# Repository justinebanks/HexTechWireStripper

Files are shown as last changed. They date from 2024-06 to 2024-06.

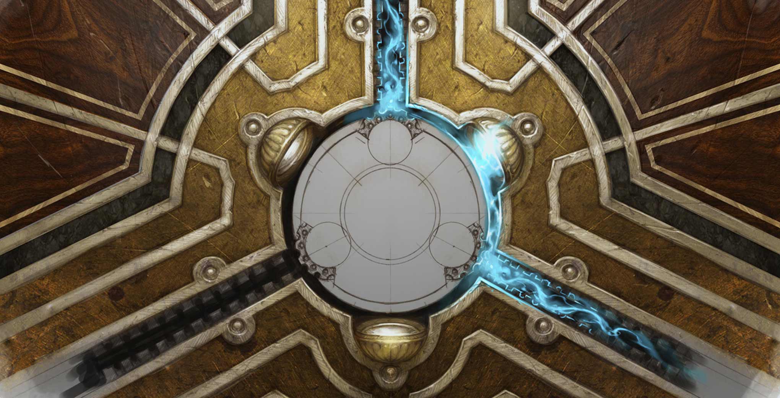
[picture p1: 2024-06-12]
src/web/HexTech_LoL.jpg

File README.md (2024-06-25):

# HexTechAutoWireStripper
---

### Explanation
This project is a machine built to automatically cut and strip wires. This project was inspired by Programming with Red's version of it, but has been changed to work with the HexTech circuit board.

### MQTT Server
The HexTech circuit board is subscribed to an [MQTT server](https://mqtt.org/) in the cloud. The software can send publish messages to the server and the HexTech board's ESP32 microcontroller will recieve it and run the command specified. In Javascript, I used the MQTT.js CDN to very easily connect to the server.

The problem, though, was that the HexTech board wouldn't recieve a command if the command string contained too many commands. To bypass this, I had to send bits of the commands separated by 2 second delays. To do this, I translated my code to Java and used Java Swing instead of HTML, CSS, & Javascript. Because of this the full finished project is within the src/java directory

### Project Organization
The src directory contains to main parts: web and java. The user interface for this project was meant to be in the form of a website, but a problem with the MQTT Server led me to switch to Java.

The src/java direcory is a Maven project that can be downloaded and built with the VSCode "Extension Pack for Java" plugin. Any YouTube tutorial on Maven in VSCode will help get you started.

The src/web directory contains the old relic that is the Javascript project. If you open it in the browser, though, you can accessGoogle Chrome's DevTools Console by pressing Ctrl+Shift+I and navigating to the console window. This gives you access to 2 important functions for debugging: ```moveTopBlade(int)``` and ```moveWire(int)```. If the 2 linear motion motors become unbalanced, it can be fixed by running ```runSerialCommand("stepper.00_move_400")``` to move the left side down to use the other 2 functions, you need to pass their output to the ```runSerialCommand(String)``` function

### Testing and Debugging
In addition to using the DevTools Console to debug, the Java Project has an MqttTester class, which is instatiating in the MqttConnector file. By running MqttConnector.java, it will open a simple GUI application where you can manually send commands to the HexTech board through the MQTT server.

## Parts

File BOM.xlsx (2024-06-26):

Name | Quantity | Price | Notes
HexTech Board | 1 | N/A | The circuit board that makes the machine compatible with the application
Small Stepper Motor | 3 | ~$15
Wooden Board | 1 | N/A | Optional. Any Board that the components can be screwed onto works
Power Source | 1 | N/A | Preferably the HexTech-designated power source, but can be anything
WORKPRO Utility Knife Blades | 1 pack | $10 (https://www.amazon.com/WORKPRO-Utility-Blades-Dispenser-100-pack/dp/B015W3AKDQ?hvadid=693128203622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) | This is the specific blade that fits into the housing
Extruder | 1 | N/A | Can be taken from a 3D printer. These can still be bought, though
Lead screw w/ Copper Nut | 2 | $33 (https://www.amazon.co.uk/dp/B07QWKG317?ref_=cm_sw_r_cp_ud_dp_JMAC4EKE28W5Z3GSZSN8) | Can be attached to the motors with shaft couplers, but are unnecessary if the motors come with one already attached
Shaft Coupler | 2 | ~$20 | Optional. Only needed if the motors don't come with pre-attached lead screws
3D Parts | 7 | N/A | Can be downloaded from the /3d_models folder

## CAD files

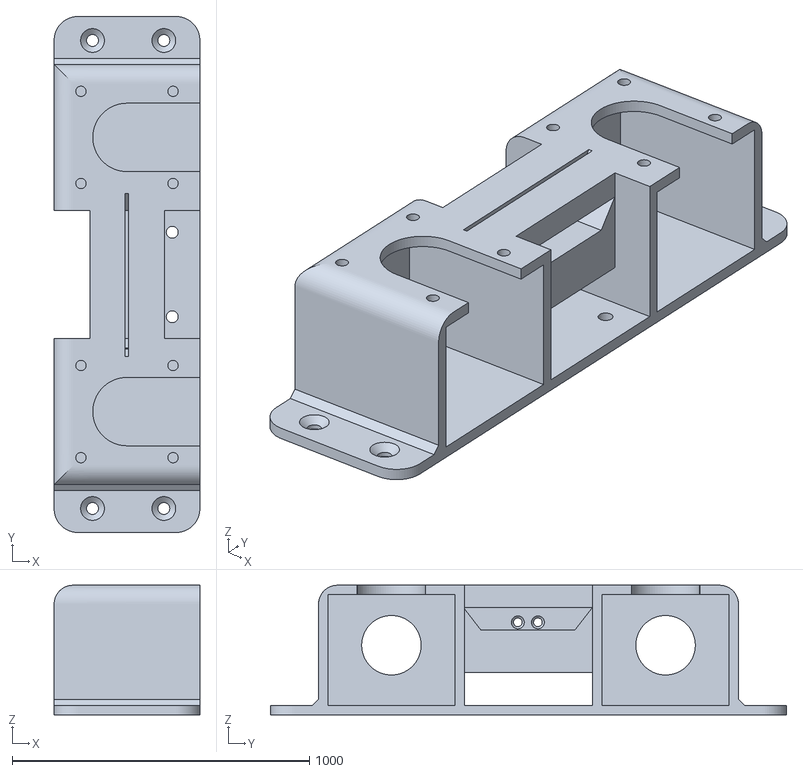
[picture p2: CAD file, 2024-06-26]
3d_models/BottomBladeHousing.stl
490.5 x 1736.0 x 436.0

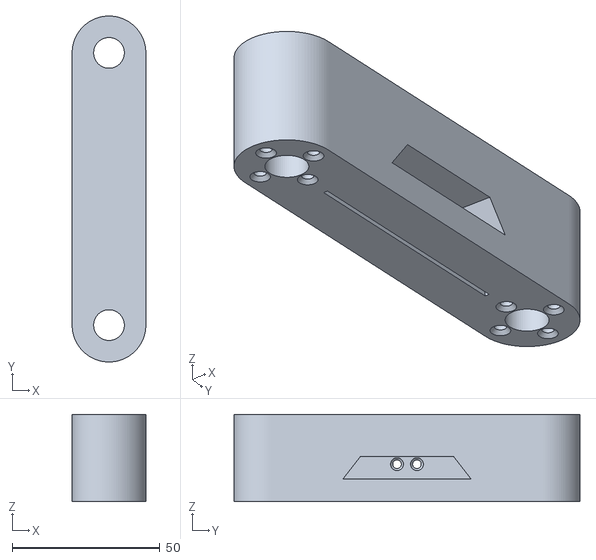
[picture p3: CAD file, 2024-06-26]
3d_models/LinearMotion_Attachment_Justin.stl
25.0 x 117.2 x 29.6

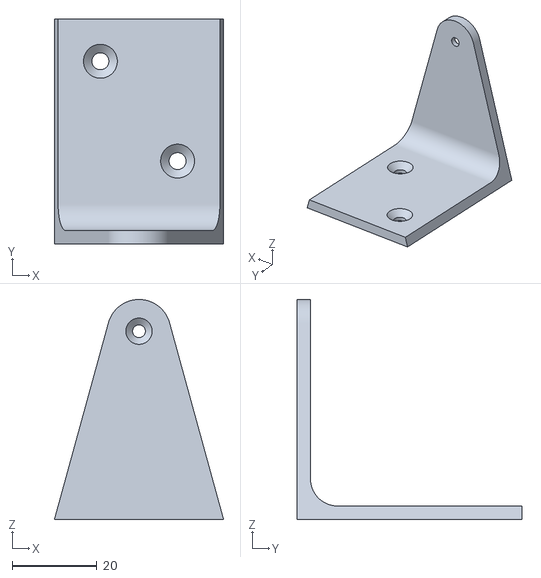
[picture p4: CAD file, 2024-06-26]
3d_models/spoolHolder_base.stl
40.0 x 53.2 x 52.0

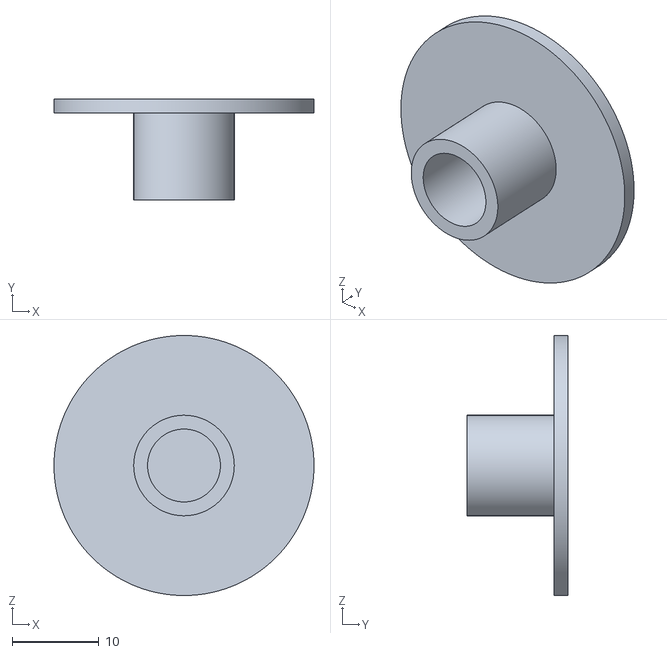
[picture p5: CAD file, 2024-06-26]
3d_models/spoolHolder_cylinder_cap.stl
30.0 x 11.6 x 30.0

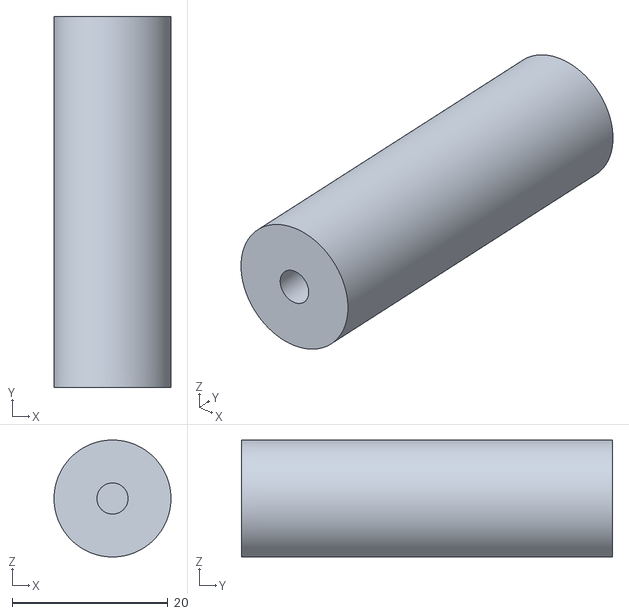
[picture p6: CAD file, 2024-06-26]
3d_models/spoolHolder_cylinder.stl
15.0 x 47.6 x 15.0

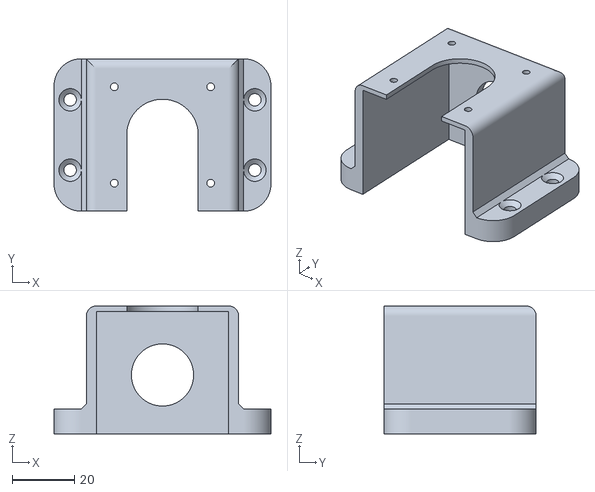
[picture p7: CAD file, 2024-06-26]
3d_models/extruderStepper_housing.stl
69.9 x 49.1 x 41.2

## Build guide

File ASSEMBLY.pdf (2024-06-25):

## Automatic Wire Cutter – Assembly Information

### Stepper Motors

This machine was built using stepper motors. Two of the stepper motors are responsible for the linear motion of the blade and the last motor powers the extruder that moves the wire forward and backward.

### 3D Printing

Most of the 3D printed parts are responsible for housing, but there are 3 spool-holding parts that are responsible for holding the spool of the wire in place. Additionally, there is a pipe glued to the back end of the extruder to keep the wire from bending away from the blade.

### HexTech Circuit Board

Each motor is connected to the HexTech circuit board on the back side of the wooden board. The program that runs the machine is set up to function correctly only if the extruder stepper is plugged into the “stepper 2” output and the stepper motors are connected (from left to right) to the “stepper 0” and “stepper 1” outputs respectively.

### Pictures

Front | Side | _

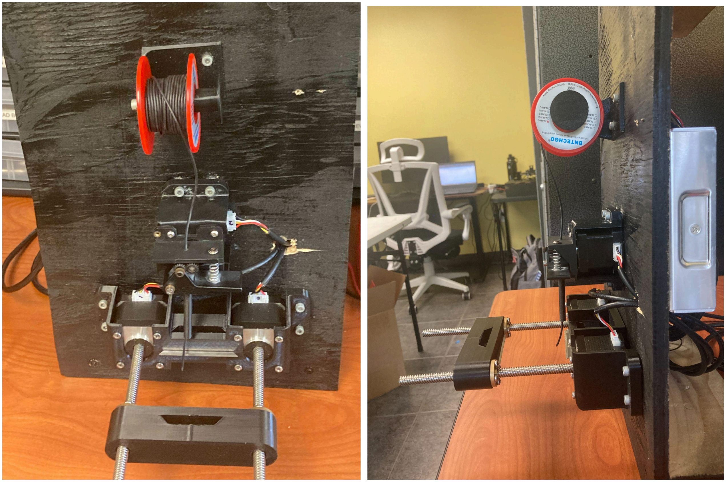
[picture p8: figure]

Back | Diagonal | _

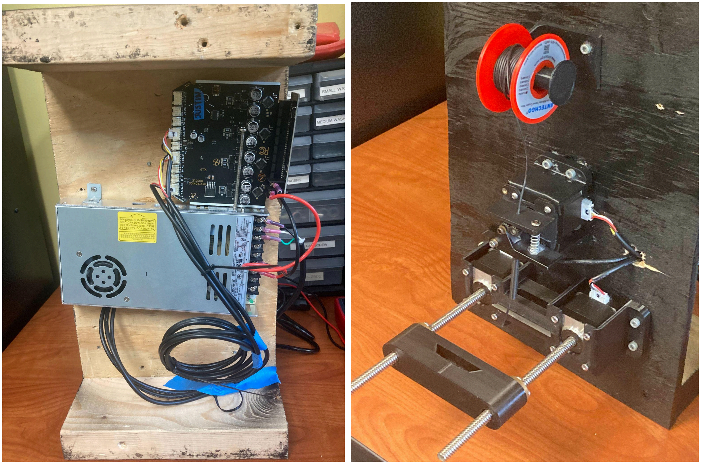
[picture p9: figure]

Wide | _

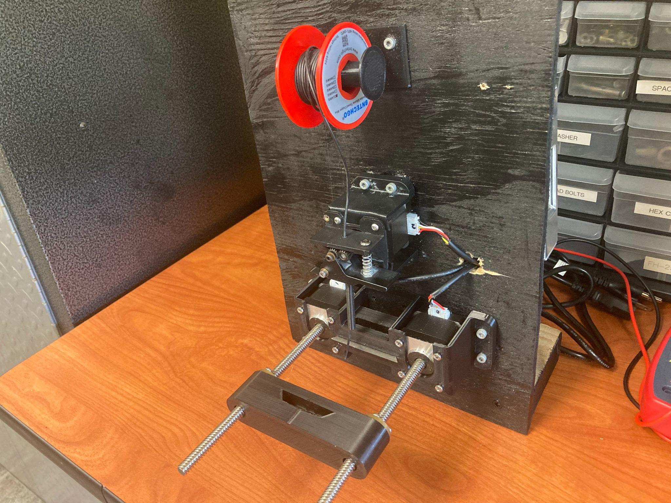
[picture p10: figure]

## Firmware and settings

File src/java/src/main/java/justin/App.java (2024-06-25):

package justin;

import javax.swing.JFrame;
import javax.swing.JTextField;
import javax.swing.SpringLayout;
import javax.swing.JButton;
import javax.swing.JLabel;

import java.awt.Dimension;
import java.awt.event.ActionEvent;
import java.awt.event.ActionListener;

import java.util.ArrayList;
import java.util.concurrent.TimeUnit;


public class App extends JFrame implements ActionListener {

    final String LIN_MOT_ONE = "stepper.00"; // rywb4-rwyb6
    final String LIN_MOT_TWO = "stepper.01"; // bwyr4-rwyb6
    final String EXTRUDER_STEPPER = "stepper.02"; // rywb4-rywb6

    final int LIN_MOT_STEP_DIST = 1;
    final int EXTRUDER_STEP_DIST = 1;
    final int BOTTOM_BLADE_POSITION = -7000;

    ArrayList<String> commandArray = new ArrayList<String>();
    ArrayList<Integer> bladeHistory = new ArrayList<Integer>();

    // MQTT Information
    MqttConnector mqtt = new MqttConnector("ws://mqtt.hextronics.cloud:8083/mqtt", "hextech-justin", "justin");
    String mqttTopic = "hextech/hextech-justin/commands";

    // Global Spring Components
    SpringLayout layout = new SpringLayout();
    JButton submitButton = new JButton("Submit");

    JTextField inputBox = new JTextField();
    JTextField leftStripLength = new JTextField("1000");
    JTextField wireLength = new JTextField("2000");
    JTextField rightStripLength = new JTextField("1000");
    JTextField stripDepth = new JTextField("150");
    JTextField wireQuantity = new JTextField("1");

    JLabel lslLabel = new JLabel("Left Strip Length:");
    JLabel wlLabel = new JLabel("Wire Length:");
    JLabel rslLabel = new JLabel("Right Strip Length:");
    JLabel sdLabel = new JLabel("Strip Depth:");
    JLabel wqLabel = new JLabel("Wire Quantity:");

    public static void main(String[] args) {
        App app = new App();
        String message = "bldc.00_move_5000";

        app.initializeCurrent();
        app.mqtt.publishMessage(app.mqttTopic, message);
        //app.runProgram();
    }


    public App() {
        this.setPreferredSize(new Dimension(540, 360));
        this.setLayout(layout);
        this.setLocationRelativeTo(null);

        Dimension preferredSize = new Dimension(200, 20);
        leftStripLength.setPreferredSize(preferredSize);
        wireLength.setPreferredSize(preferredSize);
        rightStripLength.setPreferredSize(preferredSize);
        stripDepth.setPreferredSize(preferredSize);
        wireQuantity.setPreferredSize(preferredSize);

        submitButton.addActionListener(this);

        addComponents();
        manageLayout();

        this.pack();
        this.setVisible(true);
    }


    private void manageLayout() {
        layout.putConstraint(SpringLayout.NORTH, lslLabel, 40, SpringLayout.NORTH, this);
        layout.putConstraint(SpringLayout.WEST, lslLabel, 80, SpringLayout.WEST, this);
        layout.putConstraint(SpringLayout.NORTH, leftStripLength, 0, SpringLayout.NORTH, lslLabel);
        layout.putConstraint(SpringLayout.WEST, leftStripLength, 50, SpringLayout.EAST, lslLabel);

        layout.putConstraint(SpringLayout.NORTH, wlLabel, 40, SpringLayout.NORTH, lslLabel);
        layout.putConstraint(SpringLayout.WEST, wlLabel, 0, SpringLayout.WEST, lslLabel);
        layout.putConstraint(SpringLayout.NORTH, wireLength, 0, SpringLayout.NORTH, wlLabel);
        layout.putConstraint(SpringLayout.WEST, wireLength, 0, SpringLayout.WEST, leftStripLength);

        layout.putConstraint(SpringLayout.NORTH, rslLabel, 40, SpringLayout.NORTH, wlLabel);
        layout.putConstraint(SpringLayout.WEST, rslLabel, 0, SpringLayout.WEST, lslLabel);
        layout.putConstraint(SpringLayout.NORTH, rightStripLength, 0, SpringLayout.NORTH, rslLabel);
        layout.putConstraint(SpringLayout.WEST, rightStripLength, 0, SpringLayout.WEST, leftStripLength);

        layout.putConstraint(SpringLayout.NORTH, sdLabel, 40, SpringLayout.NORTH, rslLabel);
        layout.putConstraint(SpringLayout.WEST, sdLabel, 0, SpringLayout.WEST, lslLabel);
        layout.putConstraint(SpringLayout.NORTH, stripDepth, 0, SpringLayout.NORTH, sdLabel);
        layout.putConstraint(SpringLayout.WEST, stripDepth, 0, SpringLayout.WEST, leftStripLength);

        layout.putConstraint(SpringLayout.NORTH, wqLabel, 40, SpringLayout.NORTH, sdLabel);
        layout.putConstraint(SpringLayout.WEST, wqLabel, 0, SpringLayout.WEST, lslLabel);
        layout.putConstraint(SpringLayout.NORTH, wireQuantity, 0, SpringLayout.NORTH, wqLabel);
        layout.putConstraint(SpringLayout.WEST, wireQuantity, 0, SpringLayout.WEST, leftStripLength);

        layout.putConstraint(SpringLayout.NORTH, submitButton, 50, SpringLayout.NORTH, wqLabel);
        layout.putConstraint(SpringLayout.WEST, submitButton, 0, SpringLayout.WEST, lslLabel);
    }


    private void addComponents() {
        this.add(lslLabel);
        this.add(wlLabel);
        this.add(rslLabel);
        this.add(sdLabel);
        this.add(wqLabel);

        this.add(leftStripLength);
        this.add(wireLength);
        this.add(rightStripLength);
        this.add(stripDepth);
        this.add(wireQuantity);

        this.add(submitButton);
    }


    @Override
    public void actionPerformed(ActionEvent e) {
        runProgram();
    }


    public void initializeCurrent() {
        mqtt.publishMessage(mqttTopic, "stepper.00_rms_600;stepper.01_rms_600;stepper.02_rms_200");
    }


    public void emergencyStop() {
        mqtt.publishMessage(mqttTopic, "P_stepper.00_stop;P_stepper.01_stop;P_stepper.02_stop");
    }


    public int getBladeRelativePosition() {
        int distFromHome = 0;
    
        for (int i = 0; i < bladeHistory.size(); i++) {
            distFromHome += bladeHistory.get(i);
        }
    
        return distFromHome;
    }


    public void goHome() {
        mqtt.publishMessage(mqttTopic, moveTopBlade(-getBladeRelativePosition()));
        bladeHistory.clear();
    }


    public String commandArrayToString() {
        String returnString = "";
    
        for (int i = 0; i < commandArray.size(); i++) {
            returnString = returnString + "|" + commandArray.get(i);
        }
    
        return returnString;
    }


    public String moveTopBlade(int distance) { // Positive for Up, Negative for Down
        int dist = LIN_MOT_STEP_DIST * distance;
        String command = String.format("%1$s_move_%2$d;%3$s_move_%4$d", LIN_MOT_ONE, dist*-1, LIN_MOT_TWO, dist);
    
        commandArray.add(command);
        bladeHistory.add(distance);
    
        return command;
    }


    public String moveWire(int distance) { // Positive for Forward, Negative for Backward
        int dist = EXTRUDER_STEP_DIST * distance;
        String command = String.format("%1$s_move_%2$d", EXTRUDER_STEPPER, dist);
        commandArray.add(command);
    
        return command;
    }


    public String cutWire() {
        return moveTopBlade(BOTTOM_BLADE_POSITION - getBladeRelativePosition());
    }
    
    
    public String stripWire() {
        return moveTopBlade(BOTTOM_BLADE_POSITION - getBladeRelativePosition() + Integer.parseInt(stripDepth.getText()));
    }
    
    
    public void testSequence() {
        commandArray.clear();
        moveWire(2000);
        moveTopBlade(-5000);
        moveWire(-1500);
        moveTopBlade(5000);

        mqtt.publishMessage(mqttTopic, commandArrayToString());
    }


    // Segments the full command into 3 parts and runs them separately with a 
    public void runProgram() {
        commandArray.clear();
        moveWire(Integer.parseInt(leftStripLength.getText()));
        stripWire();
        moveTopBlade(2000);
        mqtt.publishMessage(mqttTopic, commandArrayToString());

        try {
            TimeUnit.SECONDS.sleep(2);
        }
        catch (InterruptedException e) {
            System.out.println(e.getMessage());
        }
        
        commandArray.clear();
        moveWire(Integer.parseInt(wireLength.getText()));
        stripWire();
        moveTopBlade(2000);
        mqtt.publishMessage(mqttTopic, commandArrayToString());

        try {
            TimeUnit.SECONDS.sleep(2);
        }
        catch (InterruptedException e) {
            System.out.println(e.getMessage());
        }
    
        commandArray.clear();
        moveWire(Integer.parseInt(rightStripLength.getText()));
        cutWire();
        moveTopBlade(1000);
        mqtt.publishMessage(mqttTopic, commandArrayToString());

        try {
            TimeUnit.SECONDS.sleep(2);
        }
        catch (InterruptedException e) {
            System.out.println(e.getMessage());
        }

        commandArray.clear();
        moveTopBlade(6000);
        mqtt.publishMessage(mqttTopic, commandArrayToString());

    }
}

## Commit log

2024-06-12 Stepper Movement Tests and Styling Changes
2024-06-25 Adds Project Information Files
    [BOM.xlsx]
2024-06-26 Updated BOM.xlsx and added most of the 3D models
    [BOM.xlsx, extruderStepper_housing.stl, spoolHolder_base.stl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]
2024-06-26 Added the 3D models that were edited in Fusion 360
    [BottomBladeHousing.stl, LinearMotion_Attachment_Justin.stl]
